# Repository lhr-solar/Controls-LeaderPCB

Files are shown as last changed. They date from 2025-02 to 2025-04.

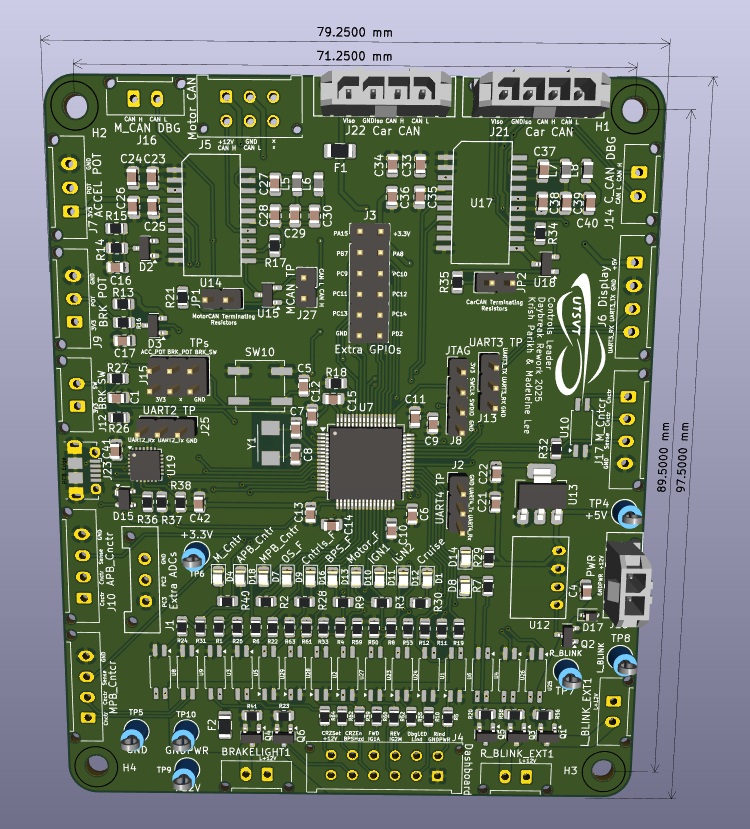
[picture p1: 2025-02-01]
Controls-Leader.png

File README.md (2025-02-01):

# Electronics : SCH/PCB
Contains all schematics and PCB files for the electrical system. Some teams may use the Solar Google Drive to upload their files.

------ 2025 Daybreak Controls Leaderboard ------
Purpose: Run main Controls code and interface with the motor controller and other systems through CAN.
Mouser link BOM: <to come>
List of components taking up volume outside of board dimensions
- Molex connectors along the entire perimeter (and one slightly inside) of the board
- Pin headers on the board
LEDs:
- Cruise controls is on
- Controls has a fault
- BPS has sent a fault
- Motor controller sent a fault
- Array precharge bypass contactor pin is high
- Motor precharge bypass contactor pin is high
- Motor contactor pin is high
-

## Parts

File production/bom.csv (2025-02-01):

Designator | Footprint | Quantity | Value | LCSC Part #
BRAKELIGHT1 | Molex_Micro-Fit_3.0_43650-0215_1x02_P3.00mm_Vertical | 1 | EXTERNAL_BRAKELIGHT
C1, C15 | 0805 | 2 | 1uF
C10, C13, C41 | 0805 | 3 | 4.7uF
C11, C12, C14, C5, C6, C9 | 0805 | 6 | 100nF
C16, C17, C24, C25, C29, C34, C35, C39, C42 | 0805 | 9 | 0.1uF
C21, C22, C4 | 0805 | 3 | 10u
C23, C28, C33, C38 | 0805 | 4 | 10uF
C26, C30, C36, C40 | 0805 | 4 | 0.01uF
C27, C37 | 0805 | 2 | 0.22uF
C7, C8 | 0805 | 2 | 12pF
D1 | 0805 | 1 | Cruise Ind
D10 | 0805 | 1 | Motor Controller Fault
D11 | 0805 | 1 | Ignition 1
D12 | 0805 | 1 | Ignition 2
D13 | 0805 | 1 | BPS Fault
D14, D8 | 0805 | 2 | PowerOn
D15 | SOT-143 | 1 | SP0503BAHTG
D16 | 0805 | 1 | Control Fault
D17 | D_SOD-323 | 1 | SD12_SOD323
D18 | 0805 | 1 | APB_CNCTR
D2, D3 | SOT-23 | 2 | BAS70-04
D4 | 0805 | 1 | M_CNCTR
D7 | 0805 | 1 | MPB_CNCTR
D9 | 0805 | 1 | OS Error
F1, F2 | 1206 | 2 | Fuse
H1, H2, H3, H4 | MountingHole_3mm | 4 | MountingHole
J1 | Molex_MicroFit3.0_1x3xP3.00mm_PolarizingPeg_Vertical | 1 | ExtraADCs
J10 | Molex_Micro-Fit_3.0_43650-0415_1x04_P3.00mm_Vertical | 1 | A_PRCHG_BYPASS
J11 | Molex_Micro-Fit_3.0_43650-0415_1x04_P3.00mm_Vertical | 1 | M_PRCHG_BYPASS
J12 | Molex_Micro-Fit_3.0_43650-0215_1x02_P3.00mm_Vertical | 1 | Brake_Sw
J13, J2, J25 | PinHeader_1x03_P2.54mm_Vertical | 3 | UART_TP
J14 | Molex_Micro-Fit_3.0_43650-0215_1x02_P3.00mm_Vertical | 1 | CAN_DB9
J15 | PinHeader_2x03_P2.54mm_Vertical | 1 | Conn_02x03_Odd_Even
J16 | Molex_Micro-Fit_3.0_43650-0215_1x02_P3.00mm_Vertical | 1 | M_CAN_DB9
J17 | Molex_Micro-Fit_3.0_43650-0415_1x04_P3.00mm_Vertical | 1 | M_CNTCTR
J18 | Molex_MicroFit3.0_1x2xP3.00mm_PolarizingPeg_Vertical | 1 | PowerConn
J21 | Molex_MicroFit3.0_1x4xP3.00mm_PolarizingPeg_Vertical | 1 | CAN_IN
J22 | Molex_MicroFit3.0_1x4xP3.00mm_PolarizingPeg_Vertical | 1 | CAN_OUT
J23 | USB_Micro-B_Molex-105017-0001 | 1 | USB_B_Micro
J27 | PinHeader_1x02_P2.54mm_Vertical | 1 | CAN_TP
J3 | PinHeader_2x06_P2.54mm_Vertical | 1 | ExtraGPIO_Conn
J4 | Molex_MicroFit3.0_2x6xP3.00mm_PolarizingPeg_Vertical | 1 | Dashboard
J5 | Molex_Micro-Fit_3.0_43045-0612_2x03_P3.00mm_Vertical | 1 | M_CAN_IN
J6 | Molex_Micro-Fit_3.0_43650-0415_1x04_P3.00mm_Vertical | 1 | Display
J7 | Molex_Micro-Fit_3.0_43650-0315_1x03_P3.00mm_Vertical | 1 | Accel_Pot
J8 | PinHeader_1x04_P2.54mm_Vertical | 1 | SWD
J9 | Molex_Micro-Fit_3.0_43650-0315_1x03_P3.00mm_Vertical | 1 | Brake_Pot
JP1, JP2 | PinHeader_1x02_P2.54mm_Vertical | 2 | Termination Resistors
L5, L6, L7, L8 | 0805 | 4 | 1.8k
LOGO1 | Hallock_Image | 1 | Dr. Hallock
LOGO2 | UTSVT_Logo_Symbol | 1 | UTSVT
LOGO4 | UTSVT_Logo_Symbol | 1 | UTSVT Logo
L_BLINK_EXT1 | Molex_Micro-Fit_3.0_43650-0215_1x02_P3.00mm_Vertical | 1 | EXTERNAL_LEFTBLINK
Q1, Q2, Q3, Q4, Q5, Q6 | SOT-23 | 6 | IRLML0030
R1, R2, R28, R3, R30, R31, R4, R40, R8, R9 | 0805 | 10 | 698
R10, R39, R5, R52, R55, R60, R62, R64 | 0805 | 8 | 2k
R11, R12, R19, R22, R6 | 0805 | 5 | 510
R13, R7 | 0805 | 2 | 5.1k
R14, R20, R23, R41, R56, R58 | 0805 | 6 | 100k
R15, R33, R50, R53, R59, R61, R63 | 0805 | 7 | 4.9k
R16, R18, R26, R27 | 0805 | 4 | 10k
R17, R34 | 0805 | 2 | 0
R21, R35 | 0805 | 2 | 120
R24, R25, R32 | 0805 | 3 | 105R
R29 | 0805 | 1 | 1.5k
R36 | 0805 | 1 | 22.1k
R37 | 0805 | 1 | 47.5k
R38 | 0805 | 1 | 1k
R_BLINK_EXT1 | Molex_Micro-Fit_3.0_43650-0215_1x02_P3.00mm_Vertical | 1 | EXTERNAL_RIGHTBLINK
SW10 | SW_SPST_B3SL-1002P | 1 | RESET
TP10 | TestPoint_Keystone_5005-5009_Compact | 1 | GND_UNISO
TP4 | TestPoint_Keystone_5005-5009_Compact | 1 | +5V_TP
TP5 | TestPoint_Keystone_5005-5009_Compact | 1 | GND_TP
TP6 | TestPoint_Keystone_5005-5009_Compact | 1 | +3.3V_TP
TP7 | TestPoint_Keystone_5005-5009_Compact | 1 | RIGHT_BLINK
TP8 | TestPoint_Keystone_5005-5009_Compact | 1 | LEFT_BLINK
TP9 | TestPoint_Keystone_5005-5009_Compact | 1 | 12V_UNISO
U1, U10, U2, U23, U24, U25, U26, U27, U28, U29, U3, U4, U5, U6, U8, U9 | SSOP-4_4.4x2.6mm_P1.27mm | 16 | EL3H7
U12 | RI3_DC_Converter | 1 | RI3-1205S
U13 | SOT-223-3_TabPin2 | 1 | NCP1117-3.3_SOT223
U14, U17 | SOIC-20W_7.5x15.4mm_Pitch1.27mm | 2 | ADM3055E
U15, U18 | SOT-23-3 | 2 | CDSOT23-T24CAN
U19 | QFN-24-1EP_4x4mm_P0.5mm_EP2.6x2.6mm | 1 | CP2102N-A01-GQFN24
U7 | LQFP-64_10x10mm_P0.5mm | 1 | STM32F413RHTx
Y1 | Crystal_SMD_TXC_7A-2Pin_5x3.2mm | 1 | Crystal

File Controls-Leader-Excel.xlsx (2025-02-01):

Reference | Value | Qty | P/N
BRAKELIGHT1,J16,L_BLINK_EXT1,R_BLINK_EXT1 | -- mixed values -- | 4 | 43650-0215
C1,C15 | 1uF | 2 | C0805C105J3RECAUTO
C4,C21,C22,C23,C28,C33,C38 | 10uF | 7 | TMK212BBJ106MGHT
C5,C6,C9,C11,C12,C14,C16,C17,C24,C25,C29,C34,C35,C39,C42 | 0.1uF | 15 | C0805C104M5R
C7,C8 | 12pF | 2 | C0805C120K5HACTU
C10,C13,C41 | 4.7uF | 3 | GRM219R6YA475KA3D
C26,C30,C36,C40 | 0.01uF | 4 | C0805C103J5RACTU
C27,C37 | 0.22uF | 2 | C0805C224J1RECTU
D1,D4,D7,D8,D9,D10,D11,D12,D13,D14,D16,D18 | -- mixed values -- | 12 | APTD2012LCGCK
D2,D3 | BAS70-04 | 2 | CDSOT23-T24CAN
D15 | SP0503BAHTG | 1 | SP0503BAHTG
D17 | SD12_SOD323 | 1 | SD12C.TCT
F1 | Fuse | 1 | 0440.375WR
F2 | Fuse | 1 | 0440003.WR
H1,H2,H3,H4,J2,J3,J8,J13,J15,J25,J27,JP1,JP2,LOGO1,LOGO2,LOGO4,TP4,TP5,TP6,TP7,TP8,TP9,TP10 | -- mixed values -- | 23
J1,J7,J9 | -- mixed values -- | 3 | 436500315
J4 | Dashboard | 1 | 430451212
J5 | M_CAN_IN | 1 | 430450626
J6,J10,J11,J17,J21,J22 | -- mixed values -- | 6 | 436500244
J12,J14,J18 | -- mixed values -- | 3 | 436500215
J23 | USB_B_Micro | 1 | 105017-1001
L5,L6,L7,L8 | 1.8k | 4 | 742792090
Q1,Q2,Q3,Q4,Q5,Q6 | IRLML0030 | 6 | IRLML0030TRPBF
R1,R2,R3,R4,R8,R9,R28,R30,R31,R40 | 698 | 10 | CR0805-FX-6980ELF
R5,R10,R39,R52,R55,R60,R62,R64 | 2k | 8 | CRCW08052K00FKEC
R6,R11,R12,R19,R22 | 510 | 5 | CRCW0805510RFKEAC
R7,R13 | 5.1k | 2 | Inventory
R14,R20,R23,R41,R56,R58 | 100k | 6 | CRCW0805100KFKEAC
R15,R33,R50,R53,R59,R61,R63 | 4.9k | 7 | CRCW08054K99FKEAC
R16,R18,R26,R27 | 10k | 4 | CRCW080510K0FKEAC
R17,R34 | 0 | 2 | CRCW08050000Z0EAC
R21,R35 | 120 | 2 | CRCW0805120RFKEA
R24,R25,R32 | 105R | 3 | CRCW0805105RFKEA
R29 | 1.5k | 1 | CRCW08051K50JNEB
R36 | 22.1k | 1 | CRCW0805-22.1K-E3
R37 | 47.5k | 1 | CRCW0805-47.5K-E3
R38 | 1k | 1 | CRCW08051K00FKEAC
SW10 | RESET | 1 | B3SL-1002P
U1,U2,U3,U4,U5,U6,U8,U9,U10,U23,U24,U25,U26,U27,U28,U29 | EL3H7 | 16 | EL3H7DTAVG
U7 | STM32F413RHTx | 1 | STM32F413RHT6
U12 | RI3-1205S | 1 | RI3-1205S
U13 | NCP1117-3.3_SOT223 | 1 | NCP1117ST33T3G
U14,U17 | ADM3055E | 2 | ADM3055E
U15,U18 | CDSOT23-T24CAN | 2 | CDSOT23-T24CAN
U19 | CP2102N-A02-GQFN24 | 1 | CP2102N-A02-GQFN24
Y1 | Crystal | 1 | ABM3-8.000MHZ-D2Y-T

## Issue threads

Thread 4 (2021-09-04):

Power Input Protection Circuitry

babusid, 2021-09-04:
During the course of testing, a power supply was plugged improperly into the controls leaderboard (+12v was connected to the ground line, and the ground was connected to the +12v line on the board), and ended up blowing the 12v->5v power regulator. We need a protection circuit ahead of the regulator in order to prevent that mistake from damaging the board.

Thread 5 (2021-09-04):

External Lights Output terminal polarity reverse

babusid, 2021-09-04:
Output Terminals on the external lights output are currently reversed in polarity and need to be flipped in the Rev 2 board.

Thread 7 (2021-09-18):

CAN2 -> CAN3

JimothyGreene, 2021-09-18:
We need to move the Motor CAN bus to use CAN3 instead of CAN2. The CAN2 design used PB12 and PB13 for Rx/Tx respectively. The new design needs to use PA8 and PA15 for Rx/Tx respectively. This will require the JTDI connection to be removed from PA15, which is not a problem since we don't actually use JTAG to program the board. We can also just remove JTDO as well while we're in this process.

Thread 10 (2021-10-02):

ADC uC pin

JimothyGreene, 2021-10-02:
Remap ADC pins. New potentiometer pins should be PC0:3 and switch contactors and precharge to old ADC locations.

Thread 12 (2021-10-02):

isoSPI Driver Short

JimothyGreene, 2021-10-02:
Short between 14-16 on driver IC

Closed 2021-10-03.

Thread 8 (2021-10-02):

12V Separation

JimothyGreene, 2021-10-02:
There are 2 12V inputs to the board. One is from primary power and the other is from secondary power. They should be labeled as such.

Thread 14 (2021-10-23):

12V CAN Motor Connection

HannahSLee14, 2021-10-23:
Motor CAN Connector has iso_5V and iso_GND connected to it instead of iso_12V and iso_GND, which is required by the motor. We need to add a 12V to 12V isolated DC-DC Converter and connect the output to these to the Motor CAN Connector.

HannahSLee14, 2021-11-06:
Ideally,  the 12V to 12V isolated DC-DC Converter would be the [RI3-1212S](https://www.mouser.com/ProductDetail/RECOM-Power/RI3-1212S?qs=IbBl3rwNelNtmsZ9Y1jE4w%3D%3D) so we can use the same footprint, but we should check the specs and needs just in case.

Closed 2022-05-01.

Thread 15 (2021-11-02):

Change isoSPI -> SPI

HannahSLee14, 2021-11-02:
Since isoSPI is giving us a lot of issues, we are going to remove the chips associated with isoSPI (LTC6820 and HX1188FNL) and any components that are a part of its circuitry. We are going to send out the SPI signals instead (MISO, MOSI, CLK, CS).

** We should check the number of wires we can have in the steering wheel disconnect. **

Closed 2022-05-01.

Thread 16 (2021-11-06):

Ignition Switch Current-Limiting Resistor

JimothyGreene, 2021-11-06:
The optocouplers attached to the ignition switch circuit need current-limiting resistors in series. Look at the other uses of these optocouplers in this board for examples.

HannahSLee14, 2021-11-06:
Value on the old schematic is 540 ohms.

Closed 2022-05-01.

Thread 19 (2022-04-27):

POR circuitry

babusid, 2022-04-27:
We're having weird issues with behavior on chip reset being different than behavior on power cycle. This could be caused by chips coming on at different points in the voltage ramp after power cycle (ie. STM comes online sooner than some peripheral chips, and immediate initializations fail as a result). Including POR circuitry on the leader board would ensure that the STM only starts executing instructions once we're past a certain voltage threshold to ensure that program execution begins after all chips are on.

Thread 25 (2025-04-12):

UART, Silkscreen labeled incorrectly

KnockbackNemo, 2025-04-12:
Some of the schematic/silkscreen labels are incorrect.

Schematic: (Should probably change this on the schematic)
UART2 should be labeled as USART2
UART3 should be UART4
UART4 should be UART5

Silkscreen: (Consider labeling this on the board?)
ExtraADCs GND should be ExtraADC1 (PC2)
ExtraADCs PC2 should be PC3
ExtraADCs PC3 should be GND

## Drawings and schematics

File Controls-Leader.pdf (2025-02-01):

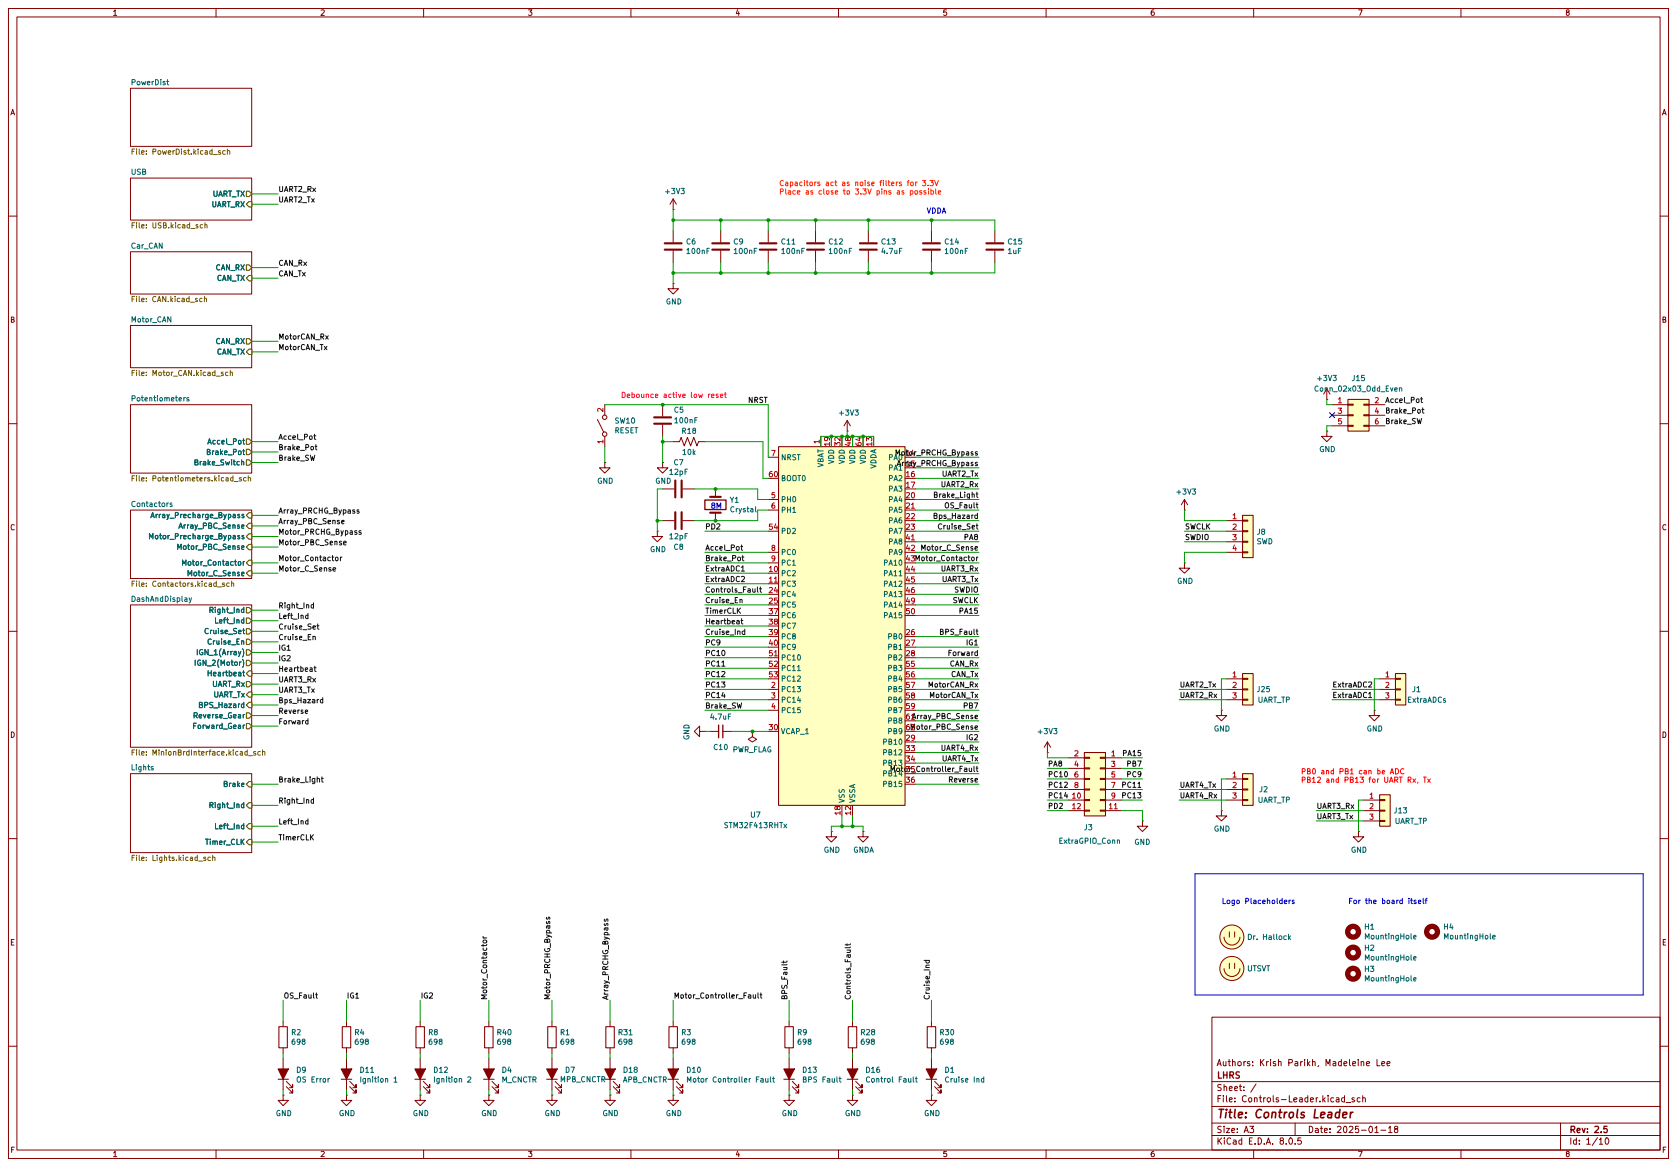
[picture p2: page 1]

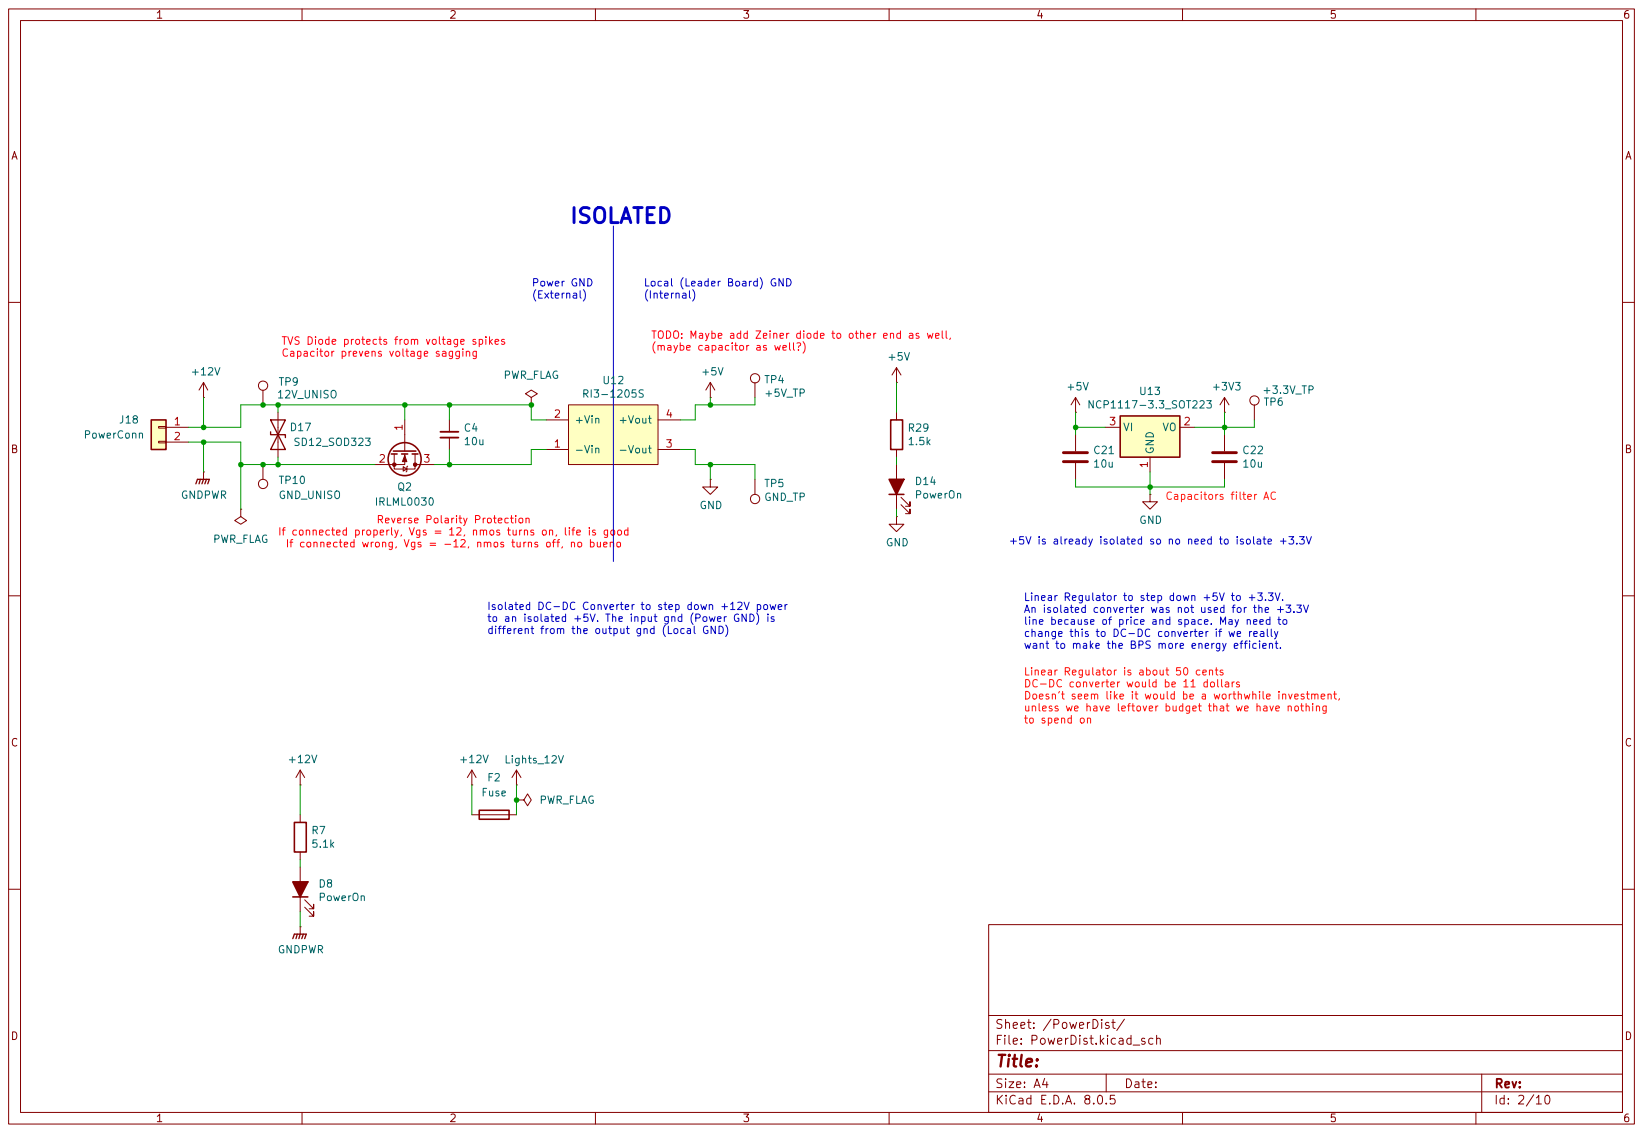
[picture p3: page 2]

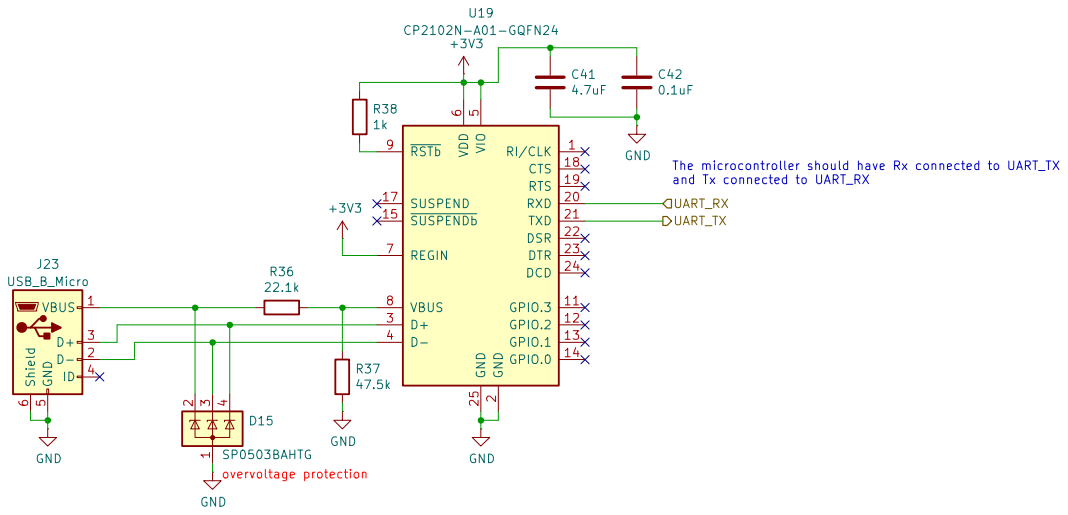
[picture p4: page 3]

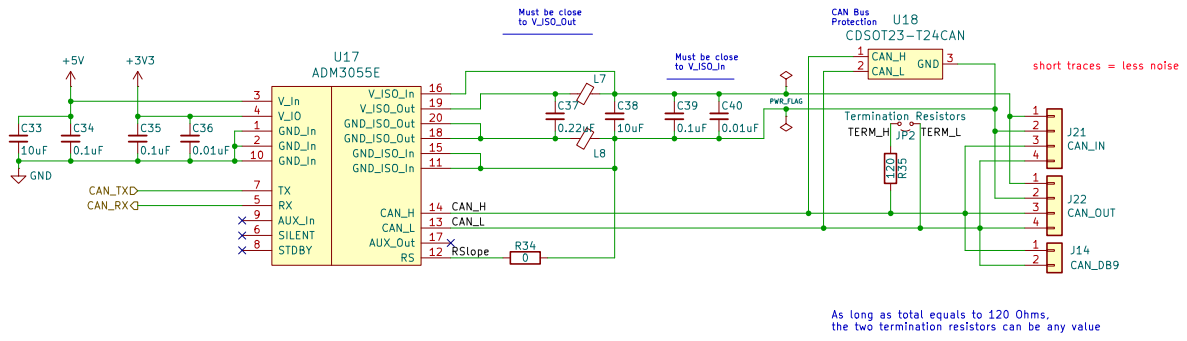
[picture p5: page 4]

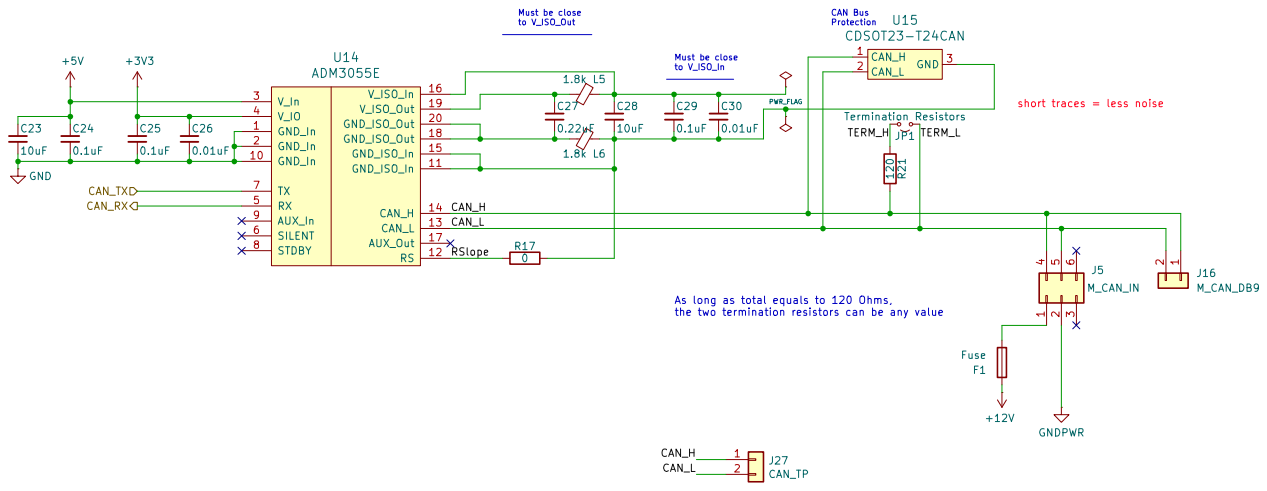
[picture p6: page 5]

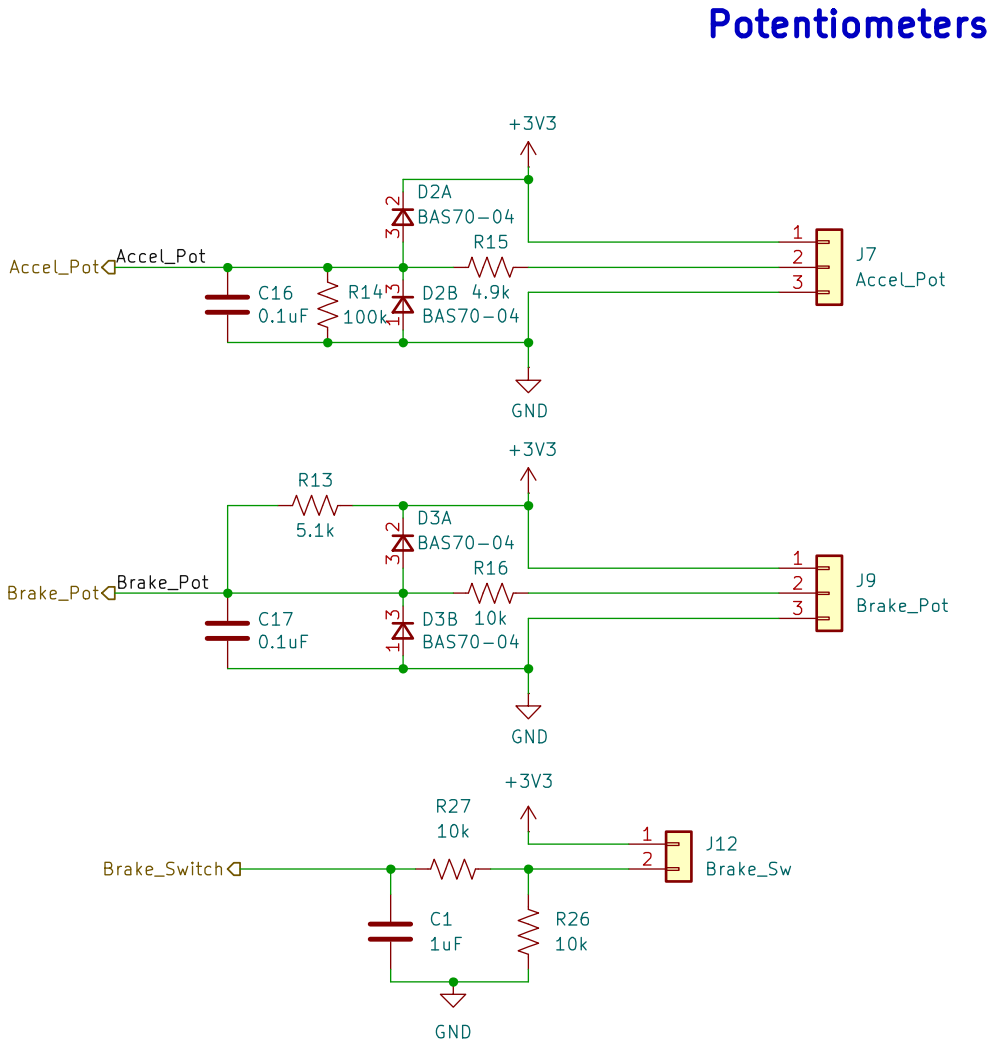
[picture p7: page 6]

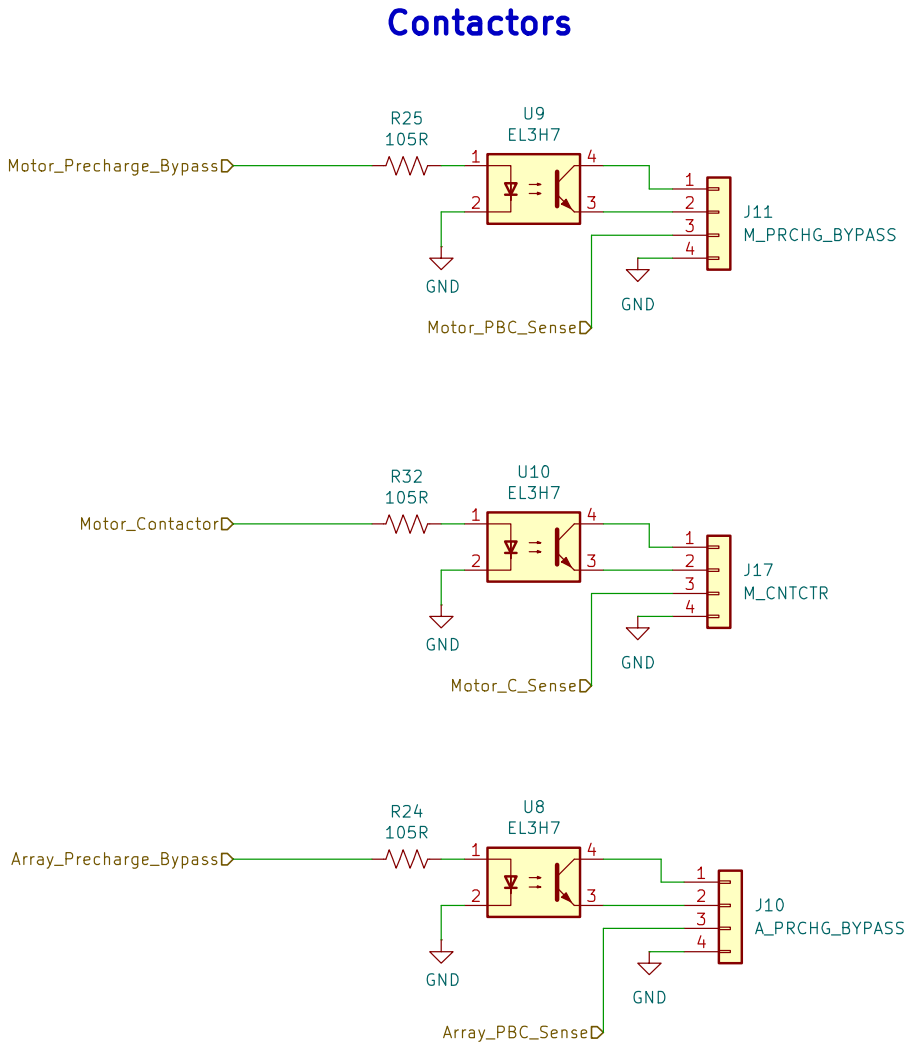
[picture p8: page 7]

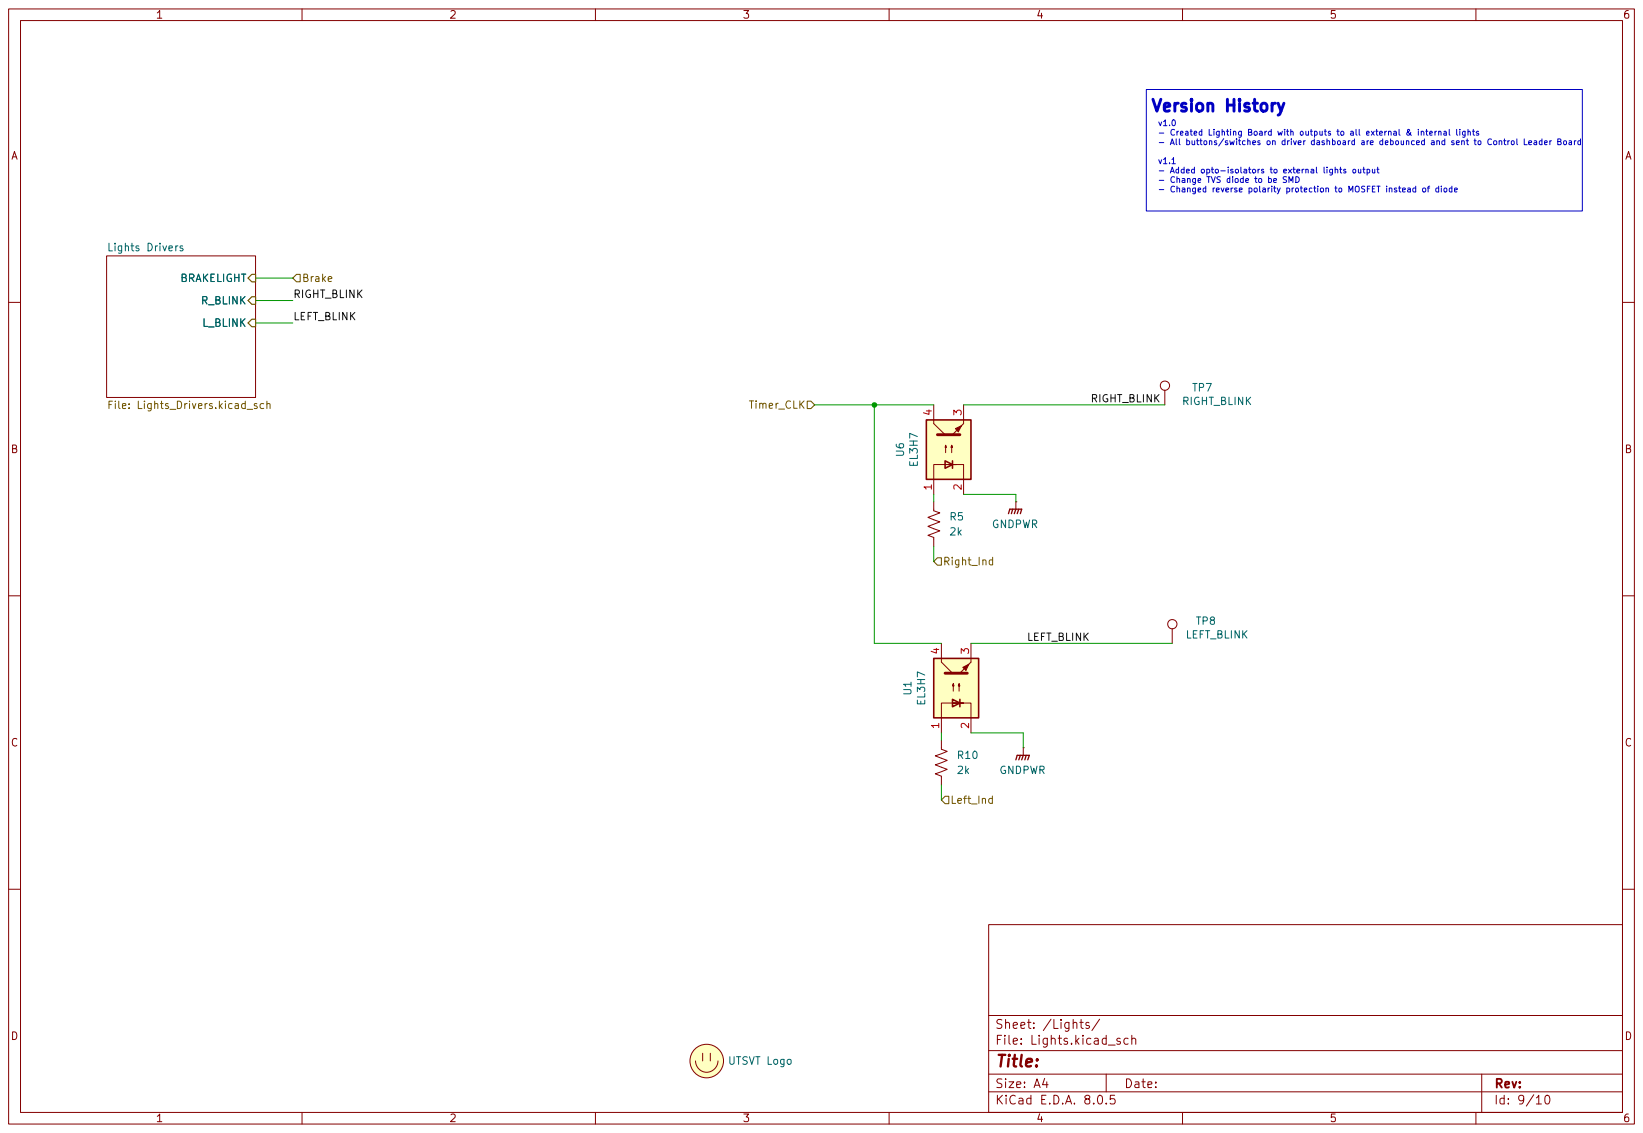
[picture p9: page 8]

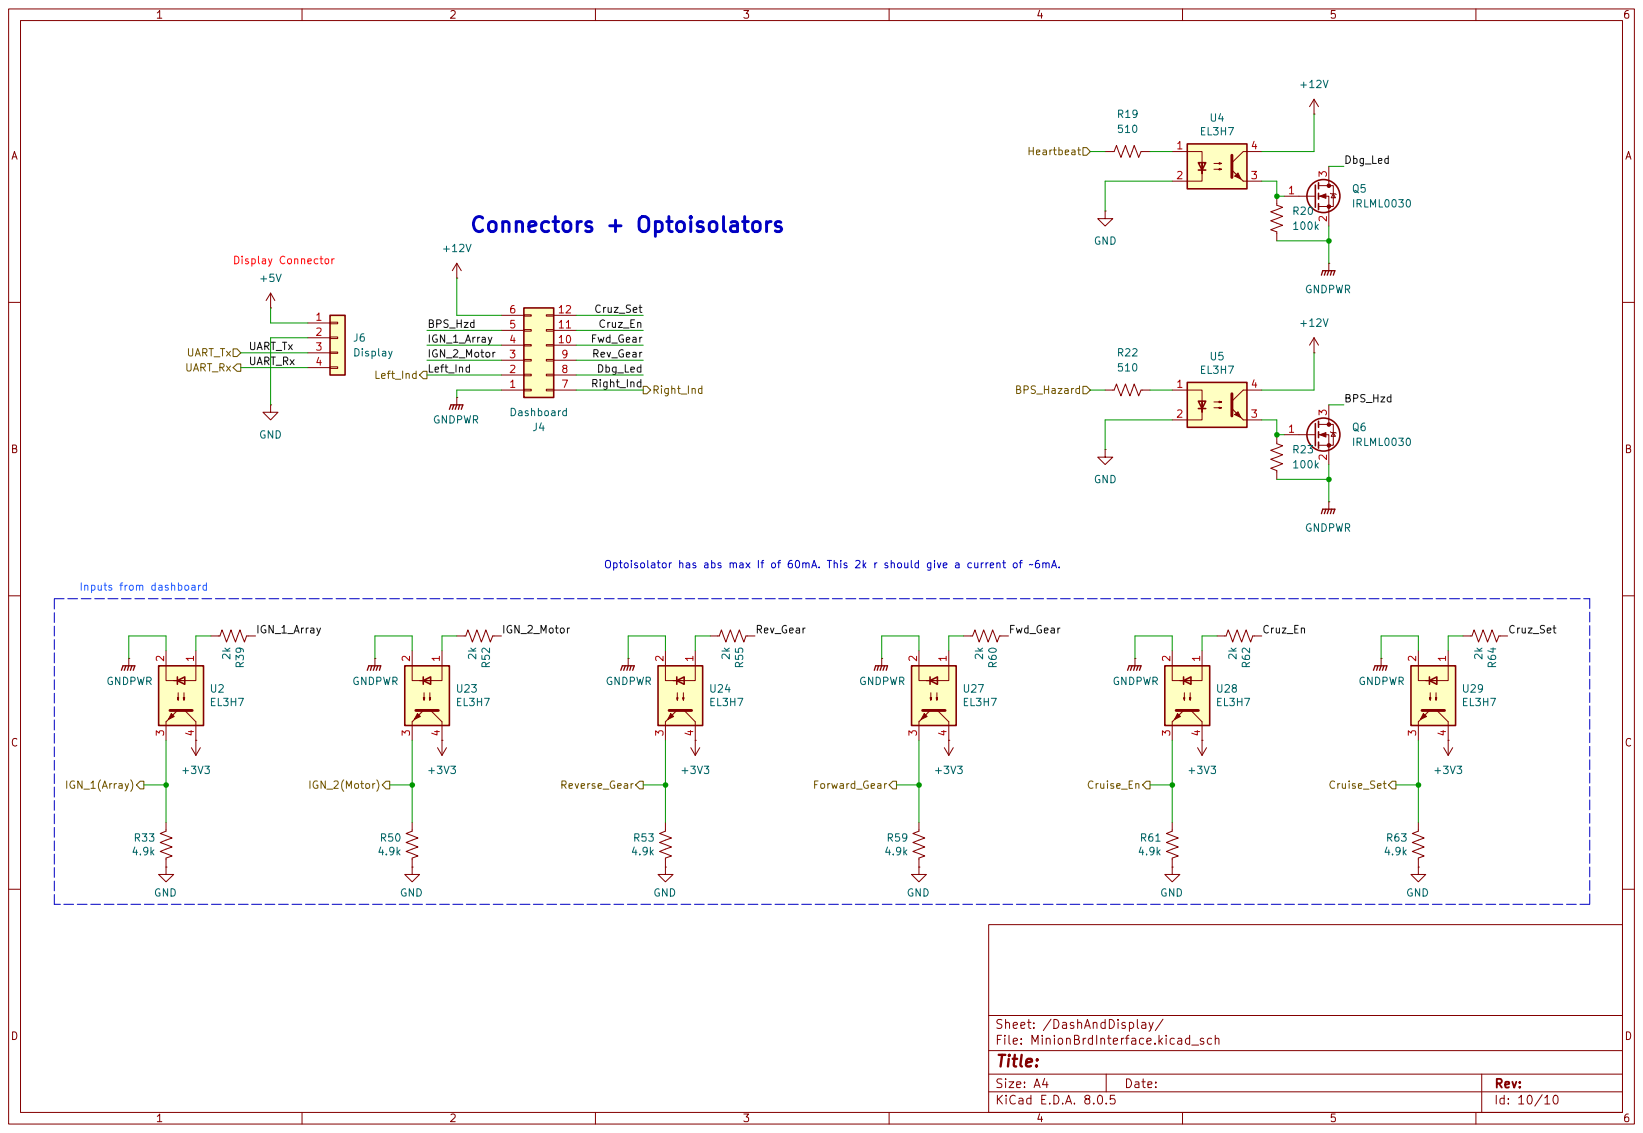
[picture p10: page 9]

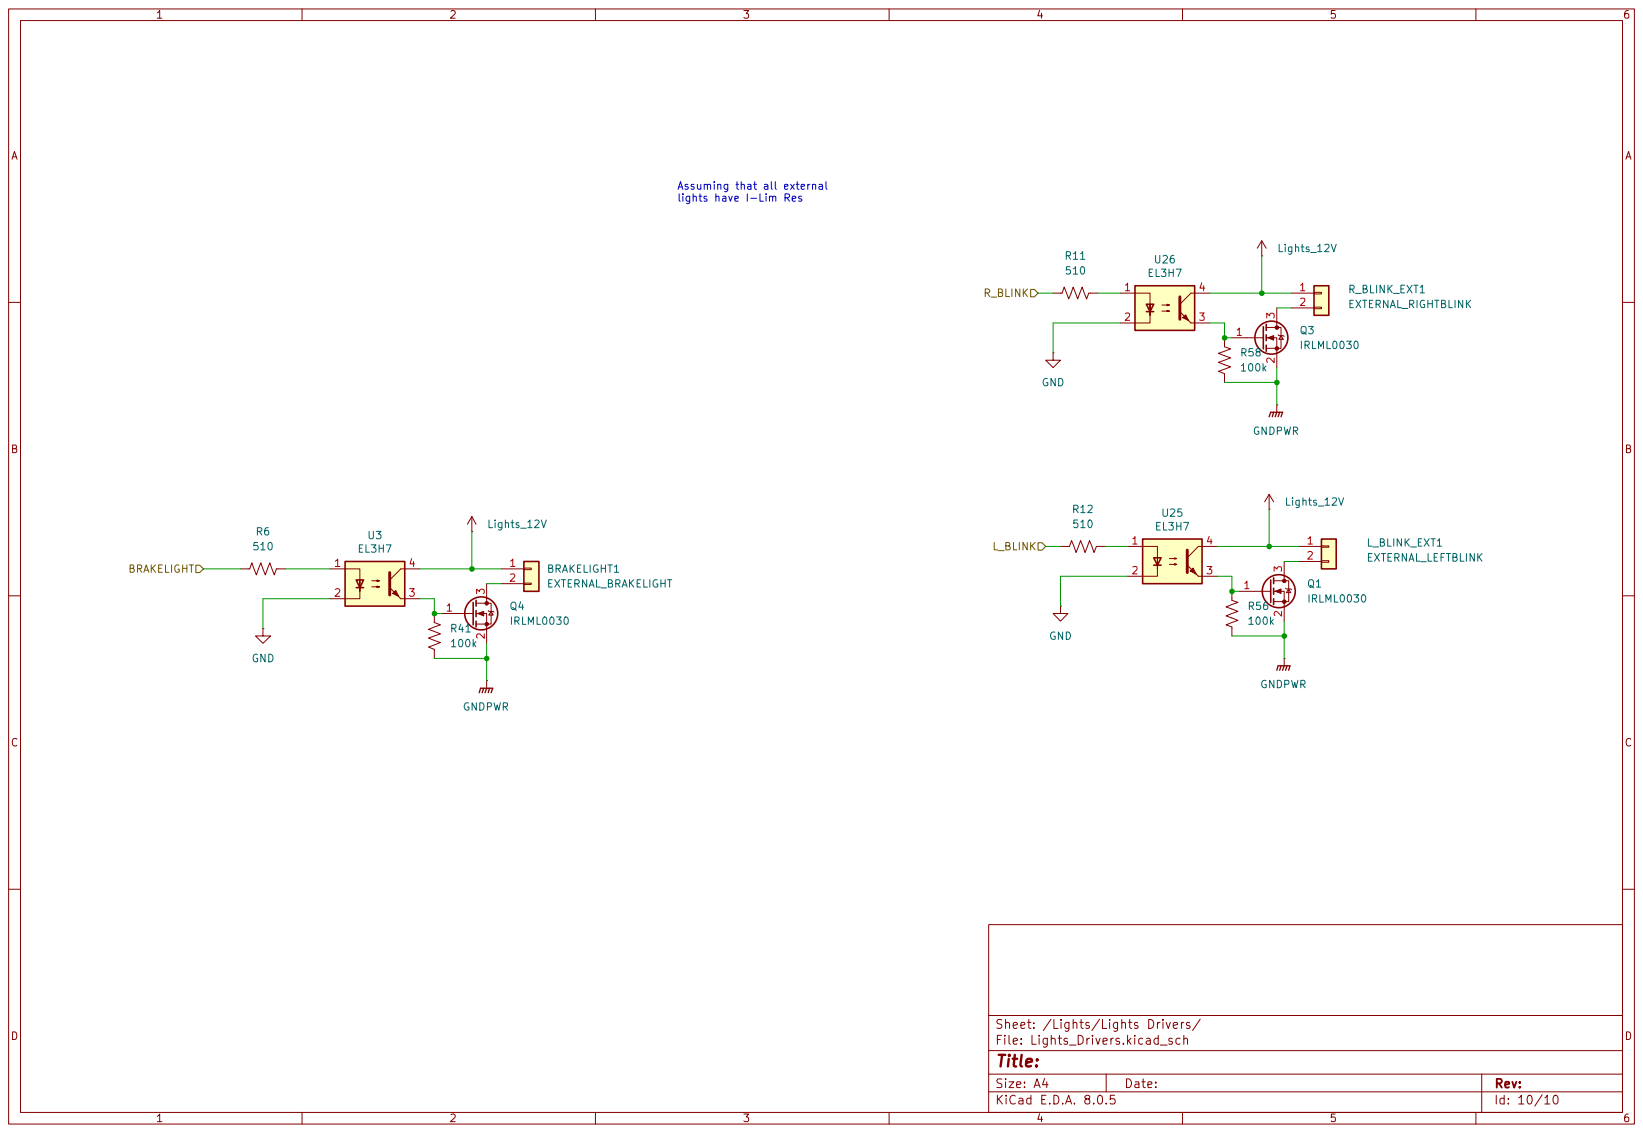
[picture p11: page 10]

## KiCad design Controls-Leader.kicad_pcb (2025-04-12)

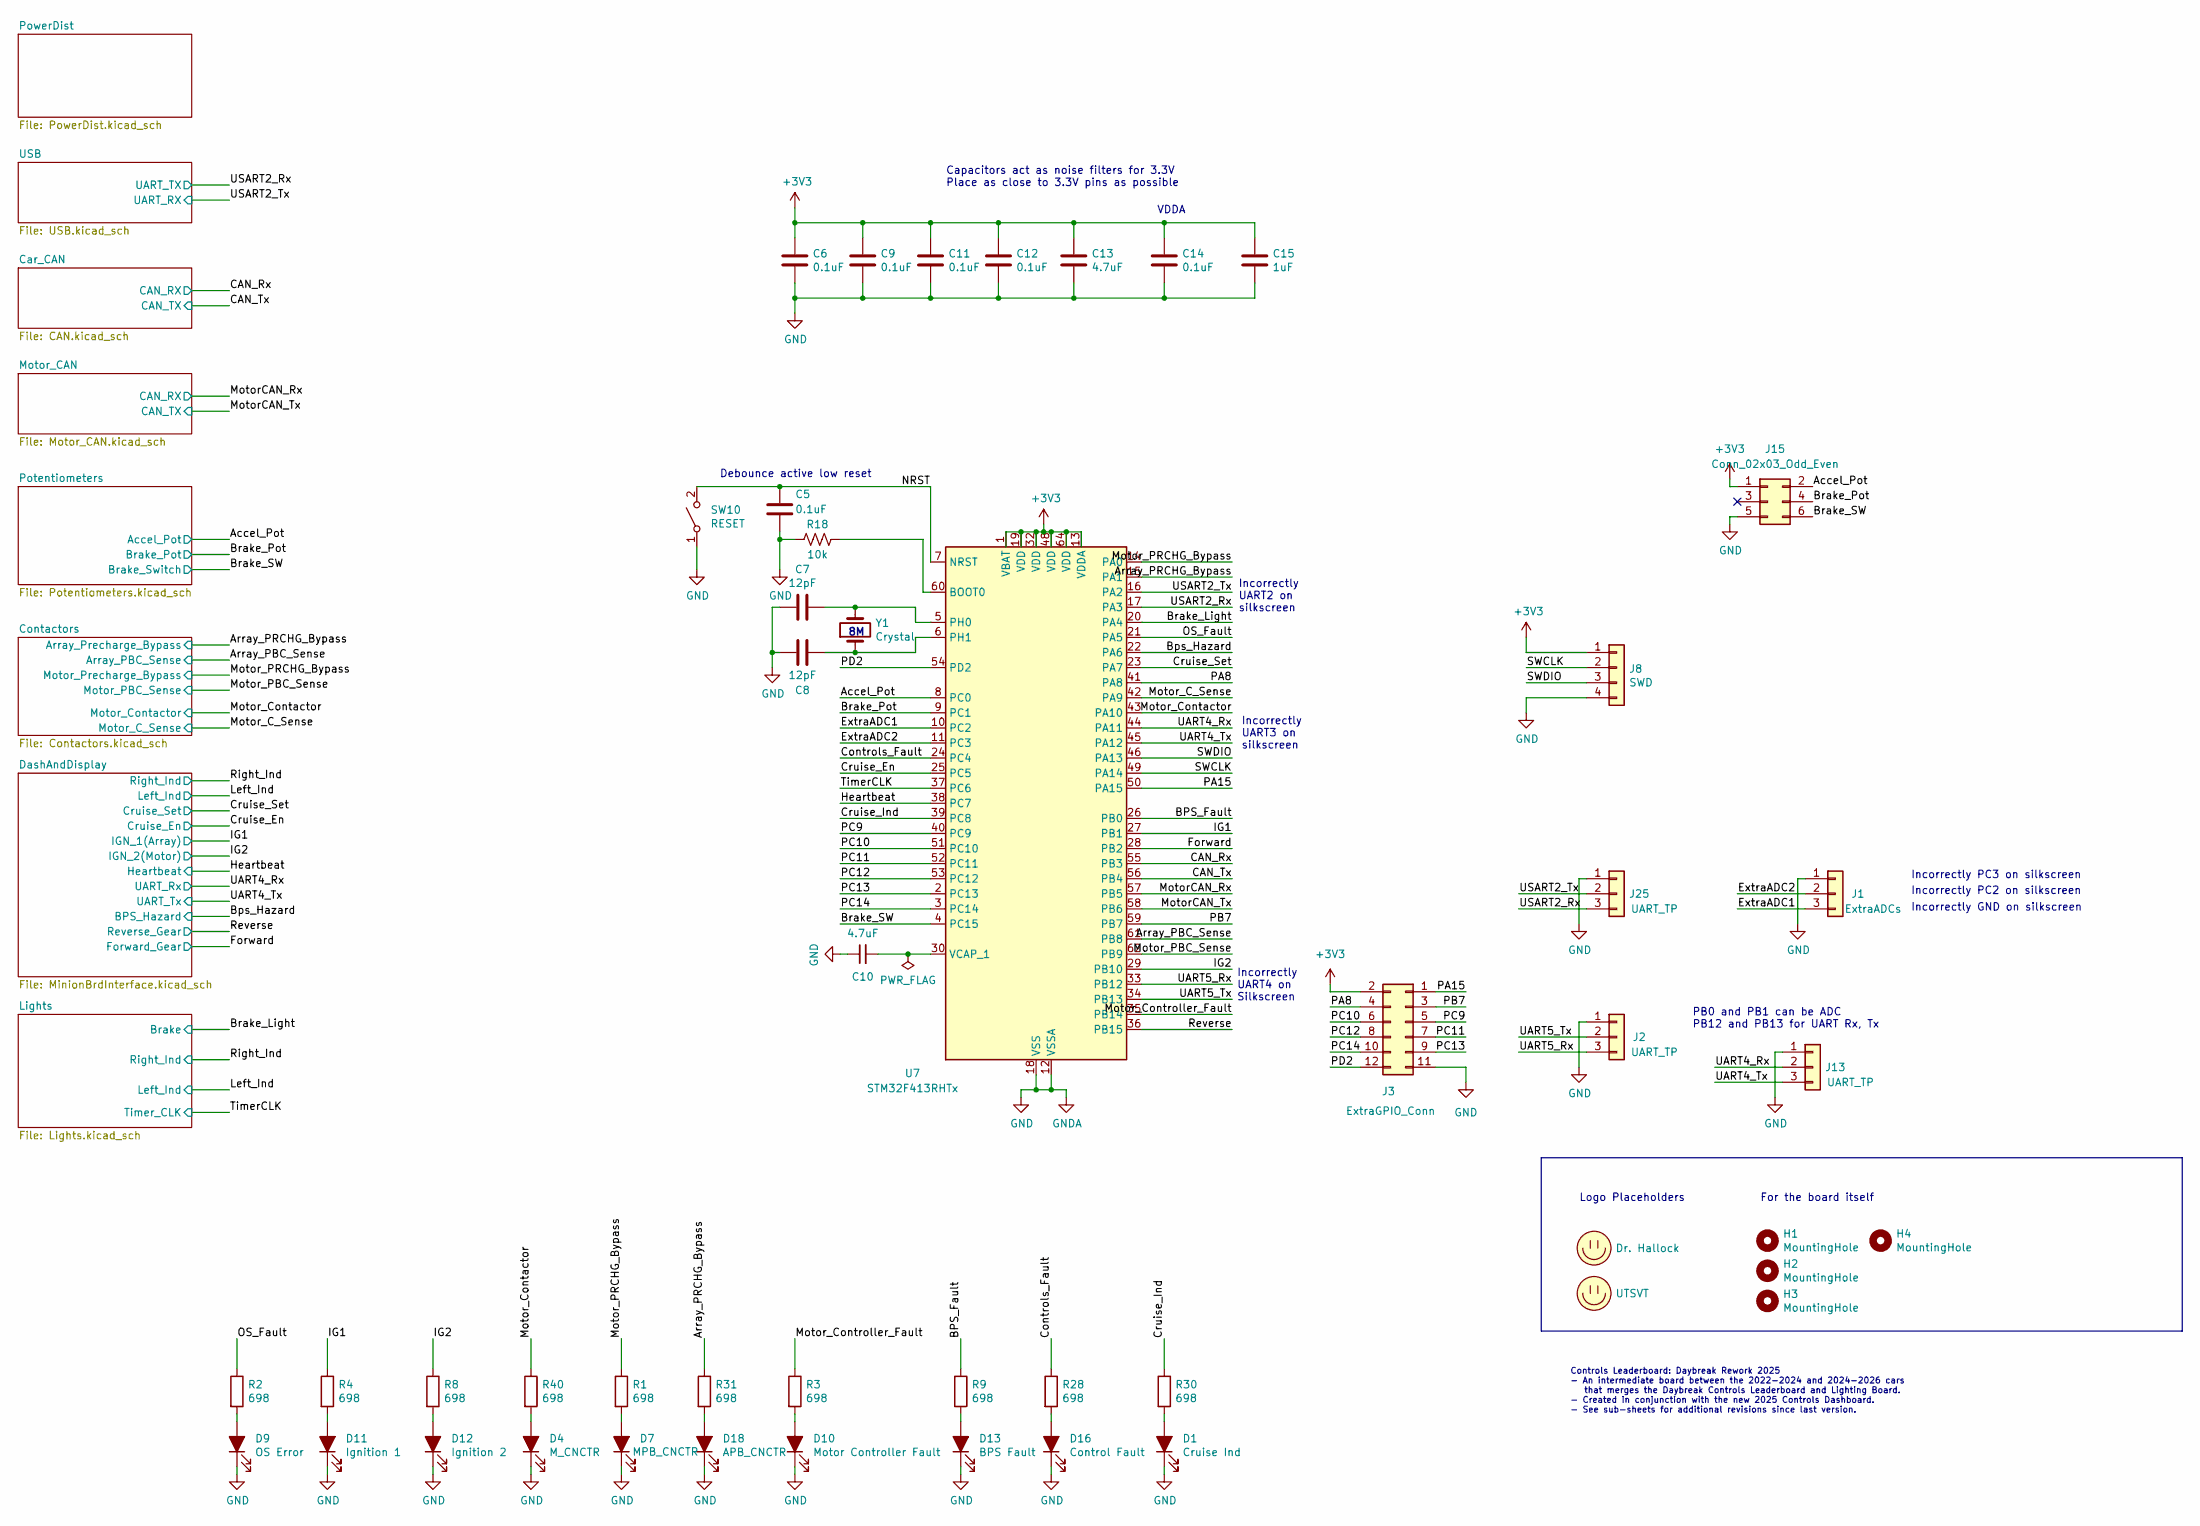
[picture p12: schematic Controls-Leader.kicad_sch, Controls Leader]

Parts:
C5, C6, C9, C11, C12, C14: 0.1uF; C_0805_2012Metric; Mouser Part Number 80-C0805C104M5R
C7, C8: 12pF; C_0805_2012Metric; Mouser Part Number 80-C0805C120K5HACTU
C10, C13: 4.7uF; C_0805_2012Metric; Mouser Part Number 81-GRM219R6YA475KA3D
C15: 1uF; C_0805_2012Metric
D1: Cruise Ind; LED_0805_2012Metric; Mouser Part Number 604-APTD2012LCGCK
D4: M_CNCTR; LED_0805_2012Metric; Mouser Part Number 604-APTD2012LCGCK
D7: MPB_CNCTR; LED_0805_2012Metric; Mouser Part Number 604-APTD2012LCGCK
D9: OS Error; LED_0805_2012Metric; Mouser Part Number 604-APTD2012LCGCK
D10: Motor Controller Fault; LED_0805_2012Metric; Mouser Part Number 604-APTD2012LCGCK
D11: Ignition 1; LED_0805_2012Metric; Mouser Part Number 604-APTD2012LCGCK
D12: Ignition 2; LED_0805_2012Metric; Mouser Part Number 604-APTD2012LCGCK
D13: BPS Fault; LED_0805_2012Metric; Mouser Part Number 604-APTD2012LCGCK
D16: Control Fault; LED_0805_2012Metric; Mouser Part Number 604-APTD2012LCGCK
D18: APB_CNCTR; LED_0805_2012Metric; Mouser Part Number 604-APTD2012LCGCK
H1, H2, H3, H4: MountingHole; MountingHole_3mm
J1: ExtraADCs; Molex_MicroFit3.0_1x3xP3.00mm_PolarizingPeg_Vertical
J2, J13, J25: UART_TP; PinHeader_1x03_P2.54mm_Vertical
J3: ExtraGPIO_Conn; PinHeader_2x06_P2.54mm_Vertical
J8: SWD; PinHeader_1x04_P2.54mm_Vertical
J15: Conn_02x03_Odd_Even; PinHeader_2x03_P2.54mm_Vertical
LOGO1: Dr. Hallock; Hallock_Image
LOGO2: UTSVT; UTSVT_Logo_Symbol
R1, R2, R3, R4, R8, R9, R28, R30, R31, R40: 698; R_0805_2012Metric; Mouser Part Number 652-CR0805FX-6980ELF
R18: 10k; R_0805_2012Metric; Mouser Part Number 71-CRCW080510K0FKEAC
SW10: RESET; SW_SPST_B3SL-1002P; Mouser Part Number 653-B3SL-1002P
U7: STM32F413RHTx; LQFP-64_10x10mm_P0.5mm; Mouser Part Number 511-STM32F413RHT6
Y1: Crystal; Crystal_SMD_TXC_7A-2Pin_5x3.2mm

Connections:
+3V3: C6.1, C9.1, C11.1, C12.1, C13.1, C14.1, C15.1, J3.2, J8.1, J15.1, U7.1 (VBAT), U7.13 (VDDA), U7.19 (VDD), U7.32 (VDD), U7.48 (VDD), U7.64 (VDD); also elsewhere on the board
/Accel_Pot: J15.2, U7.8 (PC0); also elsewhere on the board
/Array_PBC_Sense: U7.61 (PB8); also elsewhere on the board
/Array_PRCHG_Bypass: R31.1, U7.15 (PA1); also elsewhere on the board
/BPS_Fault: R9.1, U7.26 (PB0)
/Bps_Hazard: U7.22 (PA6); also elsewhere on the board
/Brake_Light: U7.20 (PA4); also elsewhere on the board
/Brake_Pot: J15.4, U7.9 (PC1); also elsewhere on the board
/Brake_SW: J15.6, U7.4 (PC15); also elsewhere on the board
/CAN_Rx: U7.55 (PB3); also elsewhere on the board
/CAN_Tx: U7.56 (PB4); also elsewhere on the board
/Controls_Fault: R28.1, U7.24 (PC4)
/Cruise_En: U7.25 (PC5); also elsewhere on the board
/Cruise_Ind: R30.1, U7.39 (PC8)
/Cruise_Set: U7.23 (PA7); also elsewhere on the board
/ExtraADC1: J1.3, U7.10 (PC2)
/ExtraADC2: J1.2, U7.11 (PC3)
/Forward: U7.28 (PB2); also elsewhere on the board
/Heartbeat: U7.38 (PC7); also elsewhere on the board
/IG1: R4.1, U7.27 (PB1); also elsewhere on the board
/IG2: R8.1, U7.29 (PB10); also elsewhere on the board
/MotorCAN_Rx: U7.57 (PB5); also elsewhere on the board
/MotorCAN_Tx: U7.58 (PB6); also elsewhere on the board
/Motor_C_Sense: U7.42 (PA9); also elsewhere on the board
/Motor_Contactor: R40.1, U7.43 (PA10); also elsewhere on the board
/Motor_Controller_Fault: R3.1, U7.35 (PB14)
/Motor_PBC_Sense: U7.62 (PB9); also elsewhere on the board
/Motor_PRCHG_Bypass: R1.1, U7.14 (PA0); also elsewhere on the board
/NRST: C5.1, SW10.2 (B), U7.7 (NRST)
/OS_Fault: R2.1, U7.21 (PA5)
/PA8: J3.4, U7.41 (PA8)
/PA15: J3.1, U7.50 (PA15)
/PB7: J3.3, U7.59 (PB7)
/PC9: J3.5, U7.40 (PC9)
/PC10: J3.6, U7.51 (PC10)
/PC11: J3.7, U7.52 (PC11)
/PC12: J3.8, U7.53 (PC12)
/PC13: J3.9, U7.2 (PC13)
/PC14: J3.10, U7.3 (PC14)
/PD2: J3.12, U7.54 (PD2)
/Reverse: U7.36 (PB15); also elsewhere on the board
/SWCLK: J8.2, U7.49 (PA14)
/SWDIO: J8.3, U7.46 (PA13)
/TimerCLK: U7.37 (PC6); also elsewhere on the board
/UART4_Rx: J13.2, U7.44 (PA11); also elsewhere on the board
/UART4_Tx: J13.3, U7.45 (PA12); also elsewhere on the board
/UART5_Rx: J2.3, U7.33 (PB12)
/UART5_Tx: J2.2, U7.34 (PB13)
/USART2_Rx: J25.3, U7.17 (PA3); also elsewhere on the board
/USART2_Tx: J25.2, U7.16 (PA2); also elsewhere on the board
GND: C5.2, C6.2, C7.2, C8.2, C9.2, C10.1, C11.2, C12.2, C13.2, C14.2, C15.2, D1.1 (K), D4.1 (K), D7.1 (K), D9.1 (K), D10.1 (K), D11.1 (K), D12.1 (K), D13.1 (K), D16.1 (K), D18.1 (K), J1.1, J2.1, J3.11, J8.4, J13.1, J15.5, J25.1, R18.2, SW10.1 (A), U7.12 (VSSA), U7.18 (VSS), U7.31 (VSS), U7.47 (VSS), U7.63 (VSS); also elsewhere on the board
unnamed: D1.2 (A), R30.2
unnamed: D4.2 (A), R40.2
unnamed: D7.2 (A), R1.2
unnamed: D9.2 (A), R2.2
unnamed: D10.2 (A), R3.2
unnamed: D11.2 (A), R4.2
unnamed: D12.2 (A), R8.2
unnamed: D13.2 (A), R9.2
unnamed: D16.2 (A), R28.2
unnamed: D18.2 (A), R31.2
unnamed: R18.1, U7.60 (BOOT0)
unnamed: C7.1, U7.5 (PH0), Y1.2
unnamed: C8.1, U7.6 (PH1), Y1.1
unnamed: C10.2, U7.30 (VCAP_1)

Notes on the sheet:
Incorrectly UART2 on silkscreen
Incorrectly GND on silkscreen
VDDA
PB0 and PB1 can be ADC PB12 and PB13 for UART Rx, Tx
Incorrectly PC3 on silkscreen
Incorrectly PC2 on silkscreen
Debounce active low reset
Incorrectly UART4 on Silkscreen
Logo Placeholders
Controls Leaderboard: Daybreak Rework 2025 - An intermediate board between the 2022-2024 and 2024-2026 cars that merges the Daybreak Controls Leaderboard and Lighting Board. - Created in conjunction with the new 2025 Controls Dashboard. - See sub-sheets for additional revisions since last version.
Incorrectly UART3 on silkscreen
Capacitors act as noise filters for 3.3V Place as close to 3.3V pins as possible
For the board itself

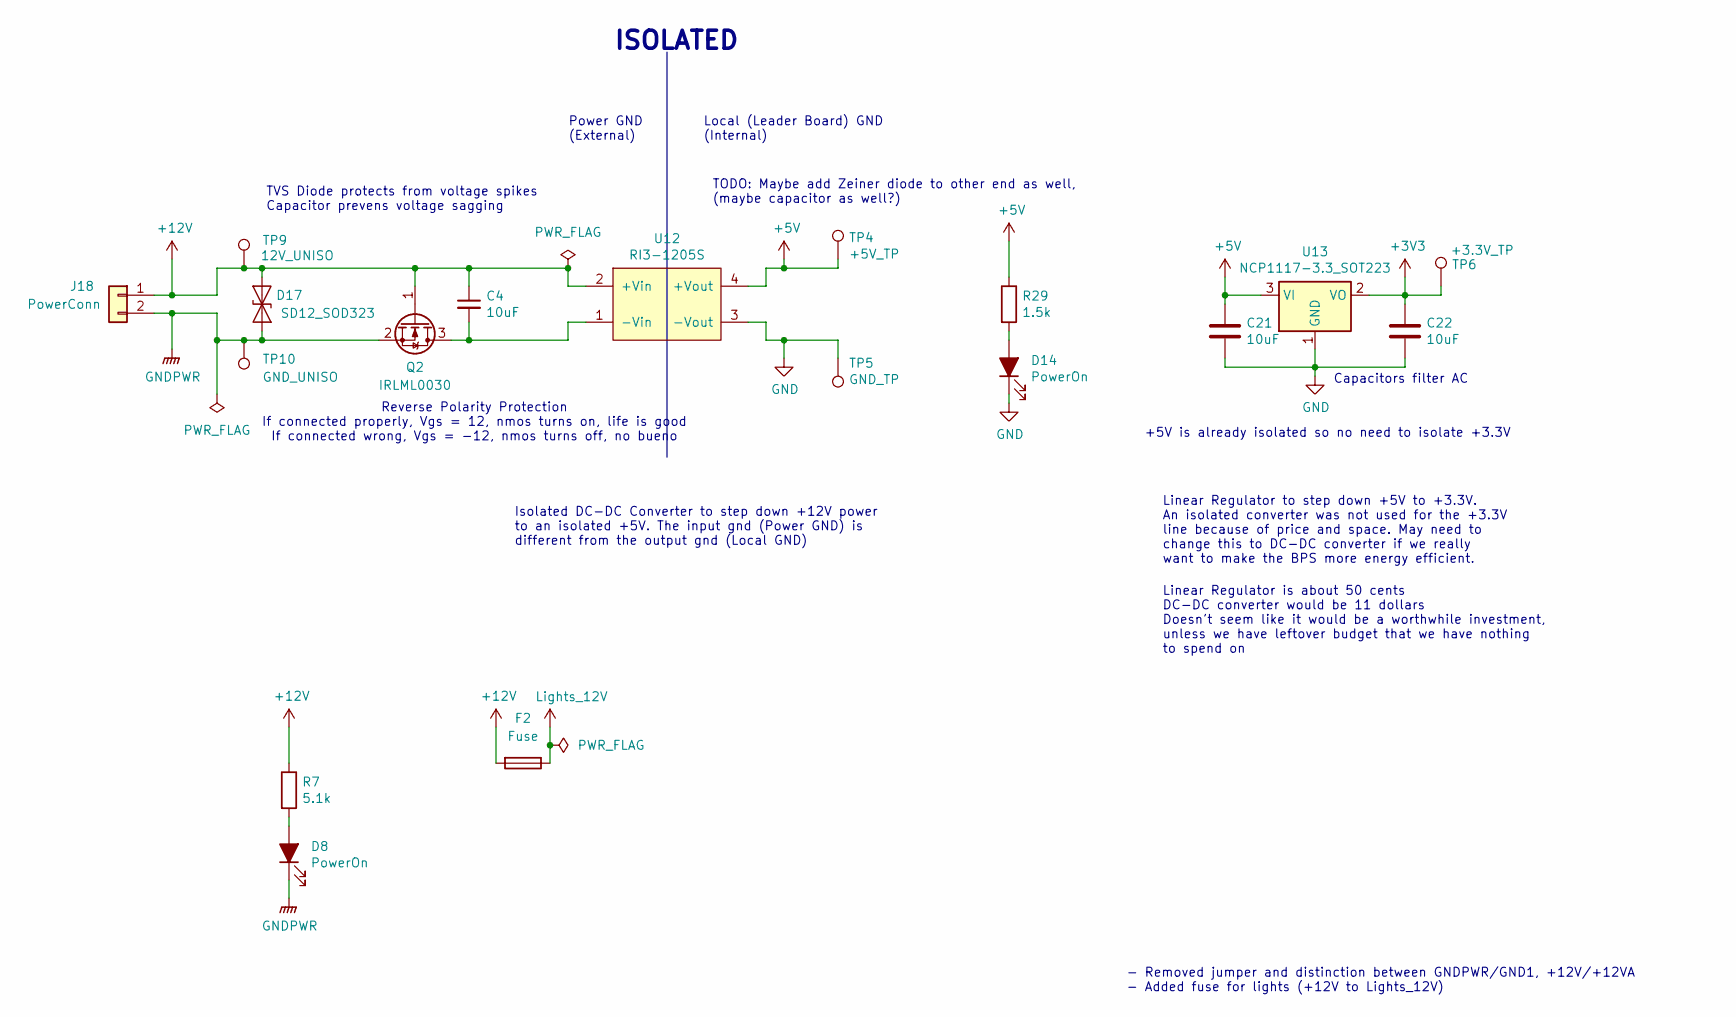
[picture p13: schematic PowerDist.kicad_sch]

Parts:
C4, C21, C22: 10uF; C_0805_2012Metric; Mouser Part Number 963-TMK212BBJ106MGHT
D8, D14: PowerOn; LED_0805_2012Metric; Mouser Part Number 604-APTD2012LCGCK
D17: SD12_SOD323; D_SOD-323
F2: Fuse; Fuse_1206_3216Metric; Mouser Part Number 576-0440003.WR
J18: PowerConn; Molex_MicroFit3.0_1x2xP3.00mm_PolarizingPeg_Vertical
Q2: IRLML0030; SOT-23
R7: 5.1k; R_0805_2012Metric
R29: 1.5k; R_0805_2012Metric; Mouser Part Number 71-CRCW08051K50JNEB
TP4: +5V_TP; TestPoint_Keystone_5005-5009_Compact
TP5: GND_TP; TestPoint_Keystone_5005-5009_Compact
TP6: +3.3V_TP; TestPoint_Keystone_5005-5009_Compact
TP9: 12V_UNISO; TestPoint_Keystone_5005-5009_Compact
TP10: GND_UNISO; TestPoint_Keystone_5005-5009_Compact
U12: RI3-1205S; RI3_DC_Converter; Mouser Part Number 919-RI3-1205S
U13: NCP1117-3.3_SOT223; SOT-223-3_TabPin2; Mouser Part Number 863-NCP1117ST33T3G

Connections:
+3V3: C22.1, TP6.1, U13.2 (VO); also elsewhere on the board
+5V: C21.1, R29.1, TP4.1, U12.4 (+Vout), U13.3 (VI); also elsewhere on the board
+12V: C4.1, D17.2 (A2), F2.2, J18.1, Q2.1 (G), R7.1, TP9.1, U12.2 (+Vin); also elsewhere on the board
GND: C21.2, C22.2, D14.1 (K), TP5.1, U12.3 (-Vout), U13.1 (GND); also elsewhere on the board
GNDPWR: D8.1 (K), D17.1 (A1), J18.2, Q2.2 (S), TP10.1; also elsewhere on the board
Lights_12V: F2.1; also elsewhere on the board
unnamed: D8.2 (A), R7.2
unnamed: D14.2 (A), R29.2
unnamed: C4.2, Q2.3 (D), U12.1 (-Vin)

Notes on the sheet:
Isolated DC-DC Converter to step down +12V power to an isolated +5V. The input gnd (Power GND) is different from the output gnd (Local GND)
TODO: Maybe add Zeiner diode to other end as well, (maybe capacitor as well?)
Linear Regulator to step down +5V to +3.3V. An isolated converter was not used for the +3.3V line because of price and space. May need to change this to DC-DC converter if we really want to make the BPS more energy efficient.
Local (Leader Board) GND (Internal)
Linear Regulator is about 50 cents DC-DC converter would be 11 dollars Doesn't seem like it would be a worthwhile investment, unless we have leftover budget that we have nothing to spend on
+5V is already isolated so no need to isolate +3.3V
Power GND (External)
ISOLATED
TVS Diode protects from voltage spikes Capacitor prevens voltage sagging
Capacitors filter AC
- Removed jumper and distinction between GNDPWR/GND1, +12V/+12VA - Added fuse for lights (+12V to Lights_12V)
Reverse Polarity Protection If connected properly, Vgs = 12, nmos turns on, life is good If connected wrong, Vgs = -12, nmos turns off, no bueno

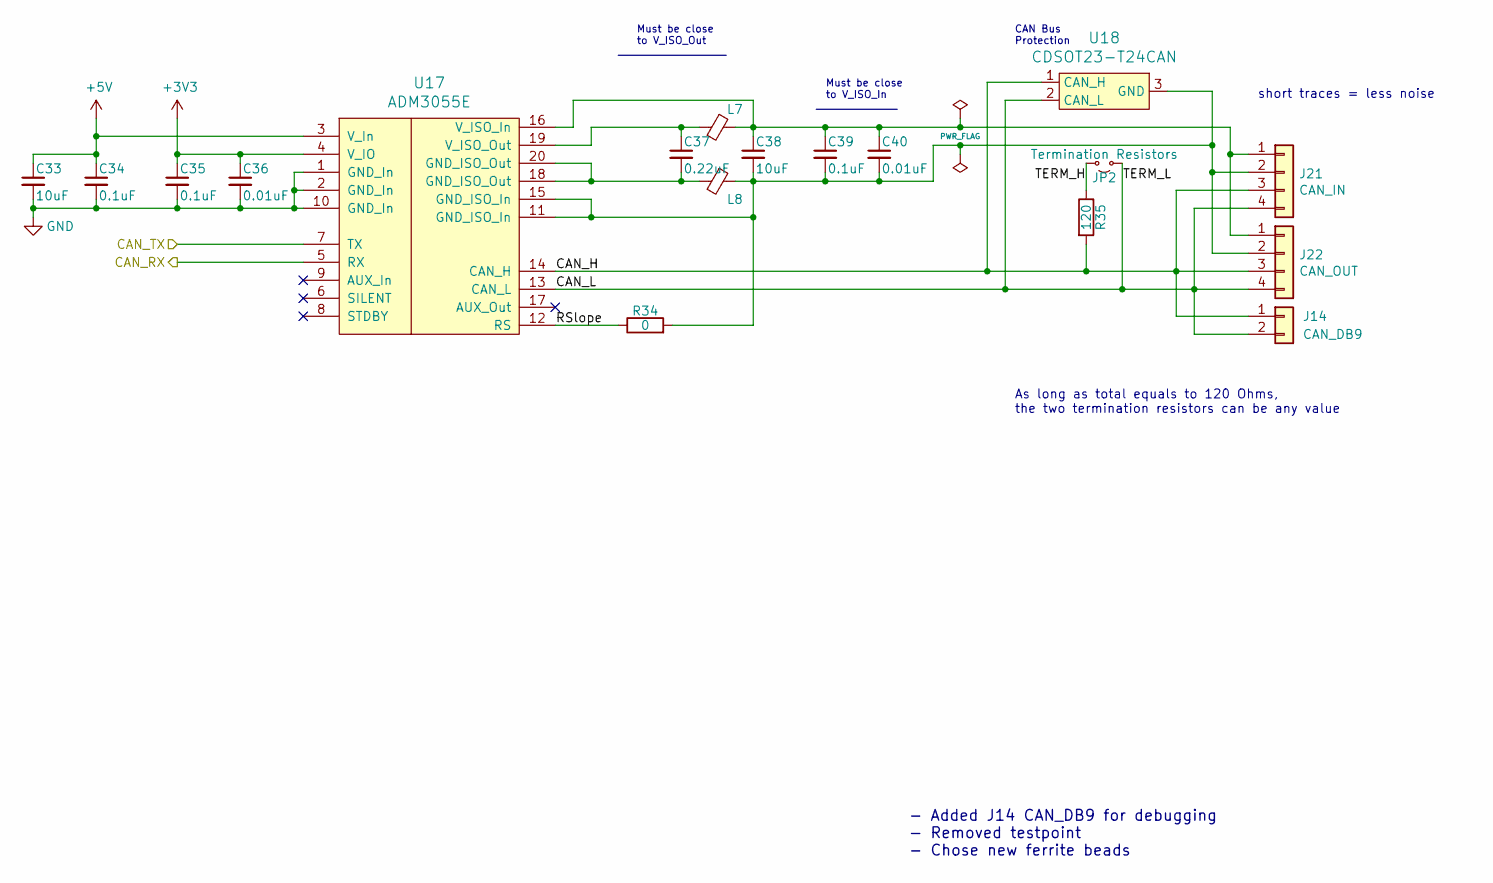
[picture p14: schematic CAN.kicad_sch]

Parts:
C33, C38: 10uF; C_0805_2012Metric; Mouser Part Number 963-TMK212BBJ106MGHT
C34, C35, C39: 0.1uF; C_0805_2012Metric; Mouser Part Number 80-C0805C104M5R
C36, C40: 0.01uF; C_0805_2012Metric
C37: 0.22uF; C_0805_2012Metric; Mouser Part Number 80-C0805C224J1RECTU
J14: CAN_DB9; Molex_Micro-Fit_3.0_43650-0215_1x02_P3.00mm_Vertical
J21: CAN_IN; Molex_MicroFit3.0_1x4xP3.00mm_PolarizingPeg_Vertical
J22: CAN_OUT; Molex_MicroFit3.0_1x4xP3.00mm_PolarizingPeg_Vertical
JP2: Termination Resistors; PinHeader_1x02_P2.54mm_Vertical
L7, L8: 1.8k; L_0805_2012Metric; Mouser Part Number 710-742792090
R34: 0; R_0805_2012Metric; Mouser Part Number 71-CRCW08050000Z0EAC
R35: 120; R_0805_2012Metric
U17: ADM3055E; SOIC-20W_7.5x15.4mm_Pitch1.27mm
U18: CDSOT23-T24CAN; SOT-23-3; Mouser Part Number 652-CDSOT23-T24CAN

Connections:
+3V3: C35.1, C36.1, U17.4 (V_IO); also elsewhere on the board
+5V: C33.1, C34.1, U17.3 (V_In); also elsewhere on the board
/CAN_Rx: U17.5 (RX); also elsewhere on the board
/CAN_Tx: U17.7 (TX); also elsewhere on the board
/Car_CAN/CAN_H: J14.1, J21.3, J22.3, R35.2, U17.14 (CAN_H), U18.1 (CAN_H)
/Car_CAN/CAN_L: J14.2, J21.4, J22.4, JP2.1 (A), U17.13 (CAN_L), U18.2 (CAN_L)
/Car_CAN/RSlope: R34.1, U17.12 (RS)
/Car_CAN/TERM_H: JP2.2 (B), R35.1
GND: C33.2, C34.2, C35.2, C36.2, U17.1 (GND_In), U17.2 (GND_In), U17.10 (GND_In); also elsewhere on the board
unnamed: C37.2, L8.2, U17.18 (GND_ISO_Out), U17.20 (GND_ISO_Out)
unnamed: C38.1, C39.1, C40.1, J21.1, J22.1, L7.1, U17.16 (V_ISO_In)
unnamed: C38.2, C39.2, C40.2, J21.2, J22.2, L8.1, R34.2, U17.11 (GND_ISO_In), U17.15 (GND_ISO_In), U18.3 (GND)
unnamed: C37.1, L7.2, U17.19 (V_ISO_Out)

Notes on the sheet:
short traces = less noise
CAN Bus Protection
As long as total equals to 120 Ohms, the two termination resistors can be any value
Must be close to V_ISO_Out
Must be close to V_ISO_In
- Added J14 CAN_DB9 for debugging - Removed testpoint - Chose new ferrite beads

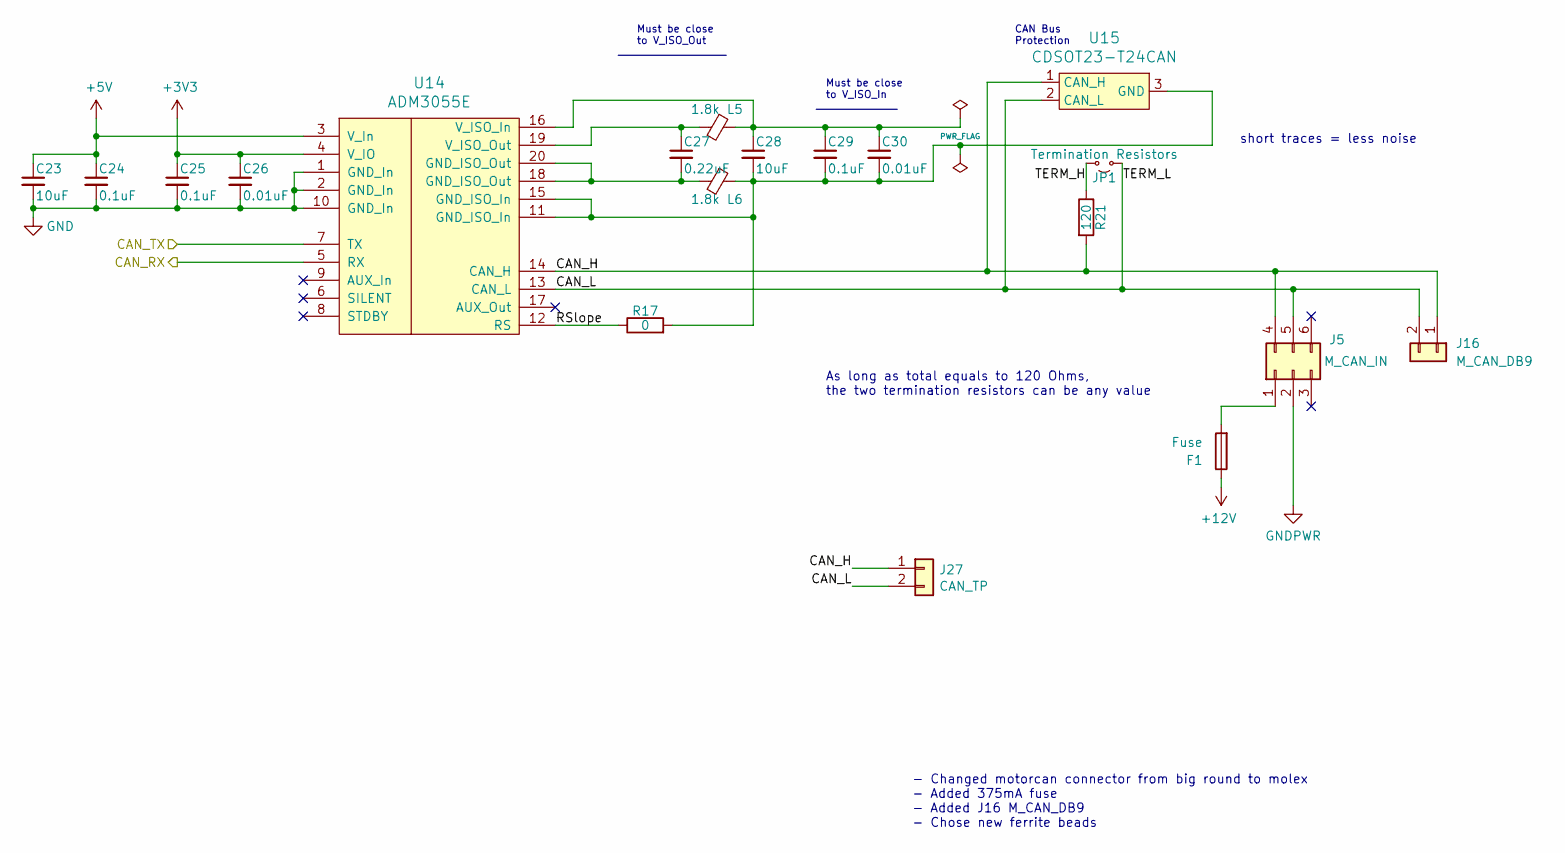
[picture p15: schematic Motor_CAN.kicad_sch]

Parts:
C23, C28: 10uF; C_0805_2012Metric; Mouser Part Number 963-TMK212BBJ106MGHT
C24, C25, C29: 0.1uF; C_0805_2012Metric; Mouser Part Number 80-C0805C104M5R
C26, C30: 0.01uF; C_0805_2012Metric
C27: 0.22uF; C_0805_2012Metric; Mouser Part Number 80-C0805C224J1RECTU
F1: Fuse; Fuse_1206_3216Metric; Mouser Part Number 576-0440.375WR
J5: M_CAN_IN; Molex_Micro-Fit_3.0_43045-0612_2x03_P3.00mm_Vertical
J16: M_CAN_DB9; Molex_Micro-Fit_3.0_43650-0215_1x02_P3.00mm_Vertical
J27: CAN_TP; PinHeader_1x02_P2.54mm_Vertical
JP1: Termination Resistors; PinHeader_1x02_P2.54mm_Vertical
L5, L6: 1.8k; L_0805_2012Metric; Mouser Part Number 710-742792090
R17: 0; R_0805_2012Metric; Mouser Part Number 71-CRCW08050000Z0EAC
R21: 120; R_0805_2012Metric
U14: ADM3055E; SOIC-20W_7.5x15.4mm_Pitch1.27mm
U15: CDSOT23-T24CAN; SOT-23-3; Mouser Part Number 652-CDSOT23-T24CAN

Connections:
+3V3: C25.1, C26.1, U14.4 (V_IO); also elsewhere on the board
+5V: C23.1, C24.1, U14.3 (V_In); also elsewhere on the board
+12V: F1.1; also elsewhere on the board
/MotorCAN_Rx: U14.5 (RX); also elsewhere on the board
/MotorCAN_Tx: U14.7 (TX); also elsewhere on the board
/Motor_CAN/CAN_H: J5.4, J16.1, J27.1, R21.2, U14.14 (CAN_H), U15.1 (CAN_H)
/Motor_CAN/CAN_L: J5.5, J16.2, J27.2, JP1.1 (A), U14.13 (CAN_L), U15.2 (CAN_L)
/Motor_CAN/RSlope: R17.1, U14.12 (RS)
/Motor_CAN/TERM_H: JP1.2 (B), R21.1
GND: C23.2, C24.2, C25.2, C26.2, U14.1 (GND_In), U14.2 (GND_In), U14.10 (GND_In); also elsewhere on the board
GNDPWR: J5.2; also elsewhere on the board
unnamed: C27.2, L6.2, U14.18 (GND_ISO_Out), U14.20 (GND_ISO_Out)
unnamed: F1.2, J5.1
unnamed: C28.1, C29.1, C30.1, L5.1, U14.16 (V_ISO_In)
unnamed: C27.1, L5.2, U14.19 (V_ISO_Out)
unnamed: C28.2, C29.2, C30.2, L6.1, R17.2, U14.11 (GND_ISO_In), U14.15 (GND_ISO_In), U15.3 (GND)

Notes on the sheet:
Must be close to V_ISO_Out
Must be close to V_ISO_In
short traces = less noise
As long as total equals to 120 Ohms, the two termination resistors can be any value
- Changed motorcan connector from big round to molex - Added 375mA fuse - Added J16 M_CAN_DB9 - Chose new ferrite beads
CAN Bus Protection

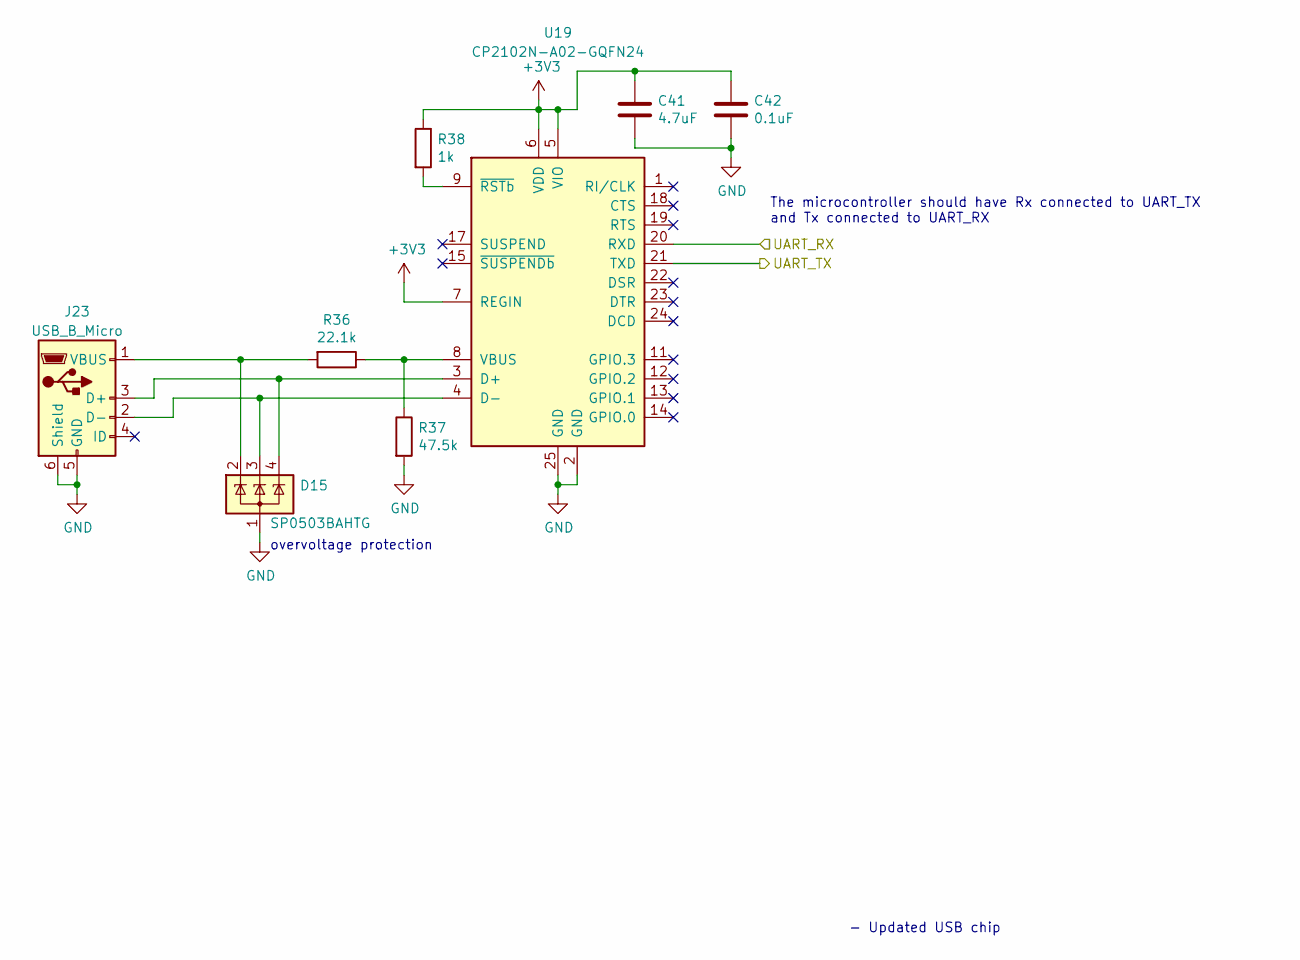
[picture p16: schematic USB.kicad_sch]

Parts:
C41: 4.7uF; C_0805_2012Metric; Mouser Part Number 81-GRM219R6YA475KA3D
C42: 0.1uF; C_0805_2012Metric; Mouser Part Number 80-C0805C104M5R
D15: SP0503BAHTG; SOT-143; Mouser Part Number 576-SP0503BAHTG
J23: USB_B_Micro; USB_Micro-B_Molex-105017-0001; Mouser Part Number 538-105017-1001
R36: 22.1k; R_0805_2012Metric; Mouser Part Number 71-CRCW0805-22.1K-E3
R37: 47.5k; R_0805_2012Metric; Mouser Part Number 71-CRCW0805-47.5K-E3
R38: 1k; R_0805_2012Metric; Mouser Part Number 71-CRCW08051K00FKEAC
U19: CP2102N-A02-GQFN24; QFN-24-1EP_4x4mm_P0.5mm_EP2.6x2.6mm; Mouser Part Number 634-CP2102NA01GQFN24

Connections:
+3V3: C41.1, C42.1, R38.1, U19.5 (VIO), U19.6 (VDD), U19.7 (REGIN); also elsewhere on the board
/USART2_Rx: U19.21 (TXD); also elsewhere on the board
/USART2_Tx: U19.20 (RXD); also elsewhere on the board
GND: C41.2, C42.2, D15.1 (A), J23.5 (GND), J23.6 (Shield), R37.2, U19.2 (GND), U19.25 (GND); also elsewhere on the board
unnamed: D15.4 (K), J23.3 (D+), U19.3 (D+)
unnamed: D15.3 (K), J23.2 (D-), U19.4 (D-)
unnamed: D15.2 (K), J23.1 (VBUS), R36.2
unnamed: R36.1, R37.1, U19.8 (VBUS)
unnamed: R38.2, U19.9 (~RSTb)

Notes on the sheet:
- Updated USB chip
The microcontroller should have Rx connected to UART_TX and Tx connected to UART_RX
overvoltage protection

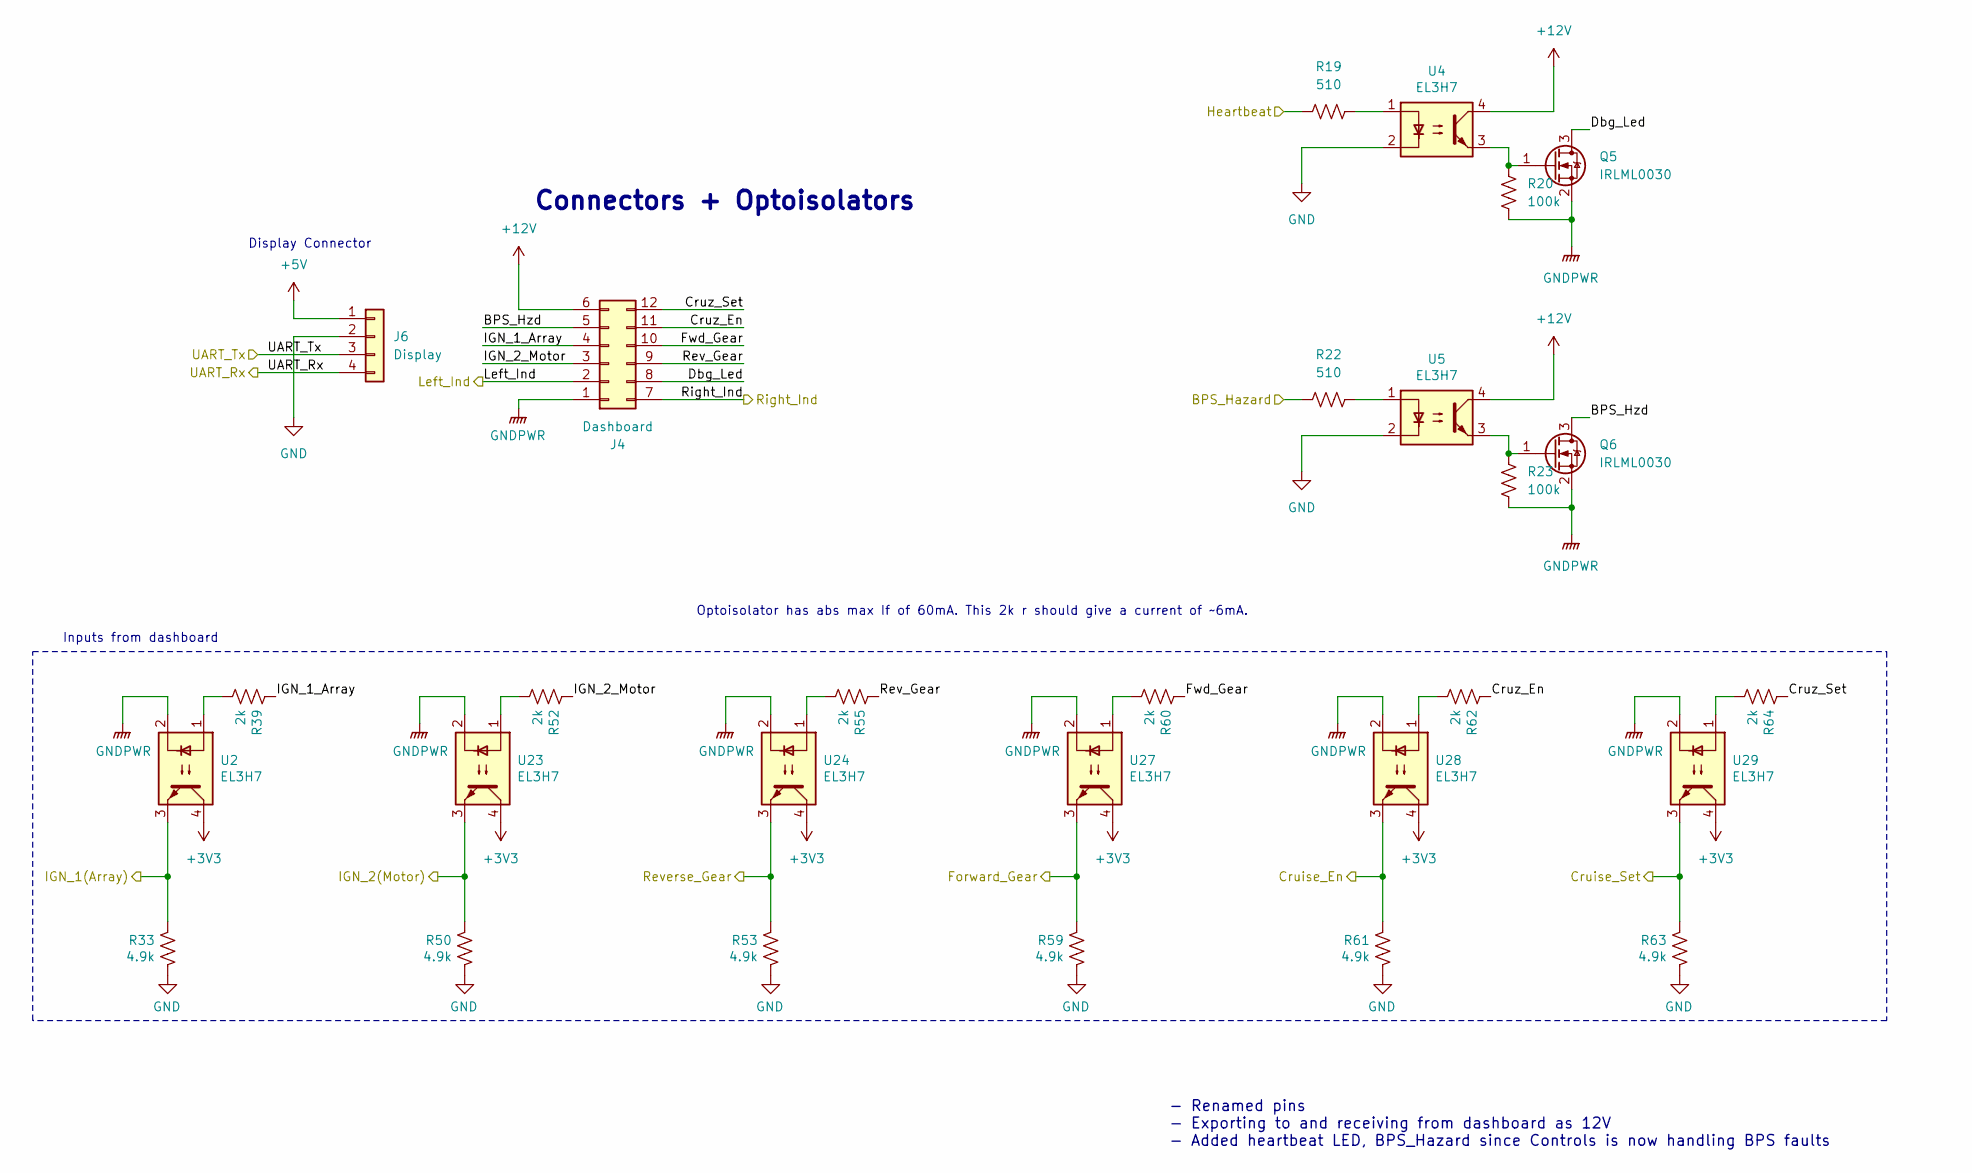
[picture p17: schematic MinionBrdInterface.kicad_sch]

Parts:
J4: Dashboard; Molex_MicroFit3.0_2x6xP3.00mm_PolarizingPeg_Vertical
J6: Display; Molex_Micro-Fit_3.0_43650-0415_1x04_P3.00mm_Vertical
Q5, Q6: IRLML0030; SOT-23
R19, R22: 510; R_0805_2012Metric; Mouser Part Number 71-CRCW0805510RFKEAC
R20, R23: 100k; R_0805_2012Metric; Mouser Part Number 71-CRCW0805100KFKEAC
R33, R50, R53, R59, R61, R63: 4.9k; R_0805_2012Metric; Mouser Part Number 71-CRCW08054K99FKEAC
R39, R52, R55, R60, R62, R64: 2k; R_0805_2012Metric; Mouser Part Number 71-CRCW08052K00FKEC
U2, U4, U5, U23, U24, U27, U28, U29: EL3H7; SSOP-4_4.4x2.6mm_P1.27mm; Mouser Part Number 638-EL3H7DTAVG

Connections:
+3V3: U2.4, U23.4, U24.4, U27.4, U28.4, U29.4; also elsewhere on the board
+5V: J6.1; also elsewhere on the board
+12V: J4.6, U4.4, U5.4; also elsewhere on the board
/Bps_Hazard: R22.1; also elsewhere on the board
/Cruise_En: R61.1, U28.3; also elsewhere on the board
/Cruise_Set: R63.1, U29.3; also elsewhere on the board
/DashAndDisplay/BPS_Hzd: J4.5, Q6.3 (D)
/DashAndDisplay/Cruz_En: J4.11, R62.1
/DashAndDisplay/Cruz_Set: J4.12, R64.1
/DashAndDisplay/Dbg_Led: J4.8, Q5.3 (D)
/DashAndDisplay/Fwd_Gear: J4.10, R60.1
/DashAndDisplay/IGN_1_Array: J4.4, R39.1
/DashAndDisplay/IGN_2_Motor: J4.3, R52.1
/DashAndDisplay/Rev_Gear: J4.9, R55.1
/Forward: R59.1, U27.3; also elsewhere on the board
/Heartbeat: R19.1; also elsewhere on the board
/IG1: R33.1, U2.3; also elsewhere on the board
/IG2: R50.1, U23.3; also elsewhere on the board
/Left_Ind: J4.2; also elsewhere on the board
/Reverse: R53.1, U24.3; also elsewhere on the board
/Right_Ind: J4.7; also elsewhere on the board
/UART4_Rx: J6.4; also elsewhere on the board
/UART4_Tx: J6.3; also elsewhere on the board
GND: J6.2, R33.2, R50.2, R53.2, R59.2, R61.2, R63.2, U4.2, U5.2; also elsewhere on the board
GNDPWR: J4.1, Q5.2 (S), Q6.2 (S), R20.2, R23.2, U2.2, U23.2, U24.2, U27.2, U28.2, U29.2; also elsewhere on the board
unnamed: Q5.1 (G), R20.1, U4.3
unnamed: Q6.1 (G), R23.1, U5.3
unnamed: R19.2, U4.1
unnamed: R22.2, U5.1
unnamed: R39.2, U2.1
unnamed: R52.2, U23.1
unnamed: R55.2, U24.1
unnamed: R60.2, U27.1
unnamed: R62.2, U28.1
unnamed: R64.2, U29.1

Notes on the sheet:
- Renamed pins - Exporting to and receiving from dashboard as 12V - Added heartbeat LED, BPS_Hazard since Controls is now handling BPS faults
Connectors + Optoisolators
Inputs from dashboard
Display Connector
Optoisolator has abs max If of 60mA. This 2k r should give a current of ~6mA.

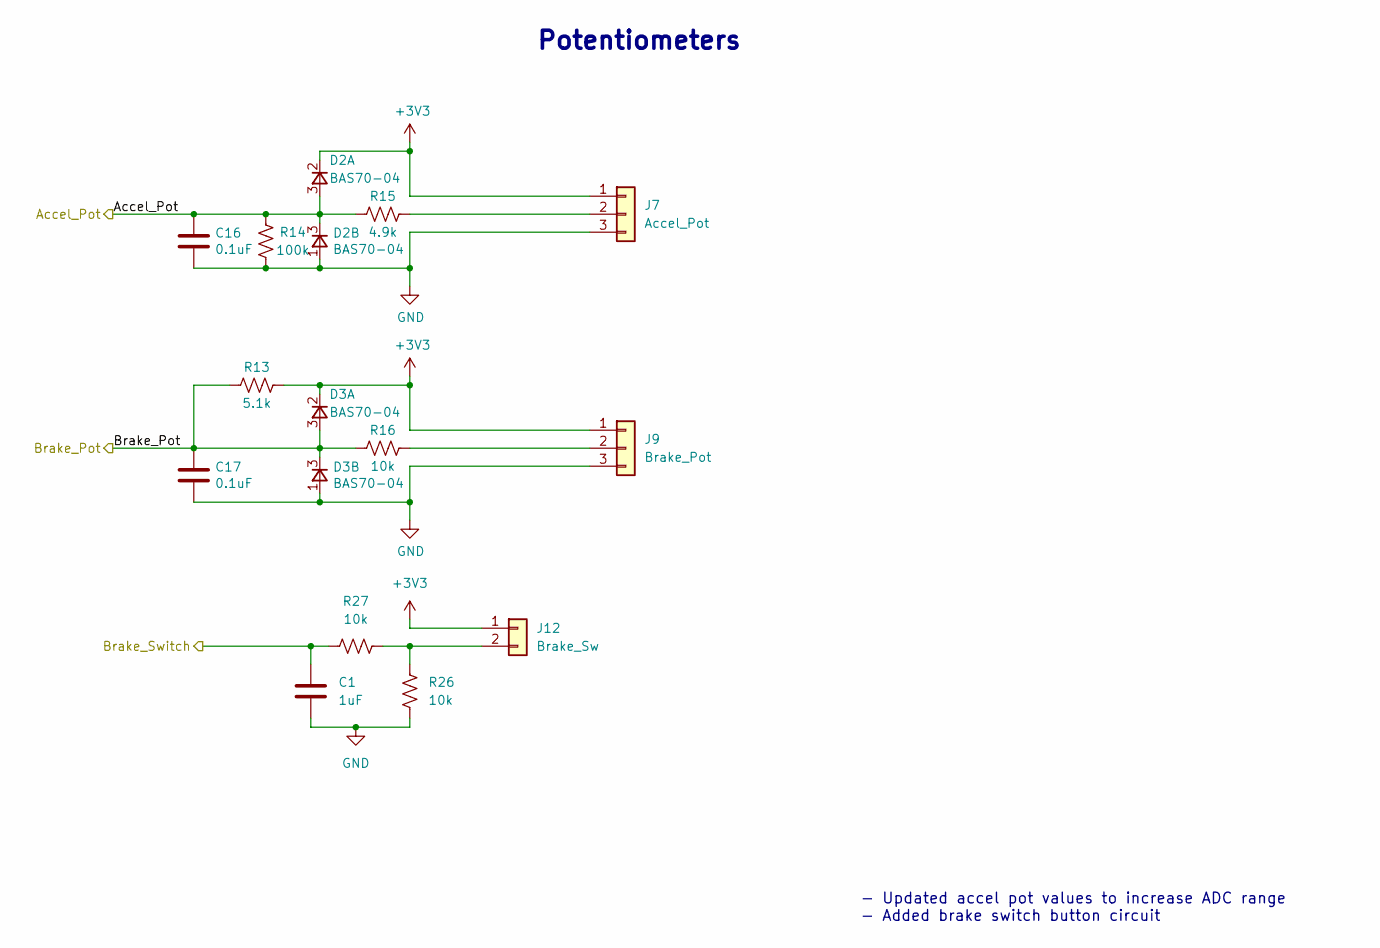
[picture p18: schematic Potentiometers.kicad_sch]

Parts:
C1: 1uF; C_0805_2012Metric
C16, C17: 0.1uF; C_0805_2012Metric; Mouser Part Number 80-C0805C104M5R
D2, D3: BAS70-04; SOT-23; Mouser Part Number 652-CDSOT23-T24CAN
J7: Accel_Pot; Molex_Micro-Fit_3.0_43650-0315_1x03_P3.00mm_Vertical
J9: Brake_Pot; Molex_Micro-Fit_3.0_43650-0315_1x03_P3.00mm_Vertical
J12: Brake_Sw; Molex_Micro-Fit_3.0_43650-0215_1x02_P3.00mm_Vertical
R13: 5.1k; R_0805_2012Metric
R14: 100k; R_0805_2012Metric; Mouser Part Number 71-CRCW0805100KFKEAC
R15: 4.9k; R_0805_2012Metric; Mouser Part Number 71-CRCW08054K99FKEAC
R16, R26, R27: 10k; R_0805_2012Metric; Mouser Part Number 71-CRCW080510K0FKEAC

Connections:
+3V3: D2.2, D3.2, J7.1, J9.1, J12.1, R13.1; also elsewhere on the board
/Accel_Pot: C16.1, D2.3, R14.1, R15.2; also elsewhere on the board
/Brake_Pot: C17.1, D3.3, R13.2, R16.2; also elsewhere on the board
/Brake_SW: C1.1, R27.1; also elsewhere on the board
GND: C1.2, C16.2, C17.2, D2.1, D3.1, J7.3, J9.3, R14.2, R26.2; also elsewhere on the board
unnamed: J7.2, R15.1
unnamed: J9.2, R16.1
unnamed: J12.2, R26.1, R27.2

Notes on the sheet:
Potentiometers
- Updated accel pot values to increase ADC range - Added brake switch button circuit

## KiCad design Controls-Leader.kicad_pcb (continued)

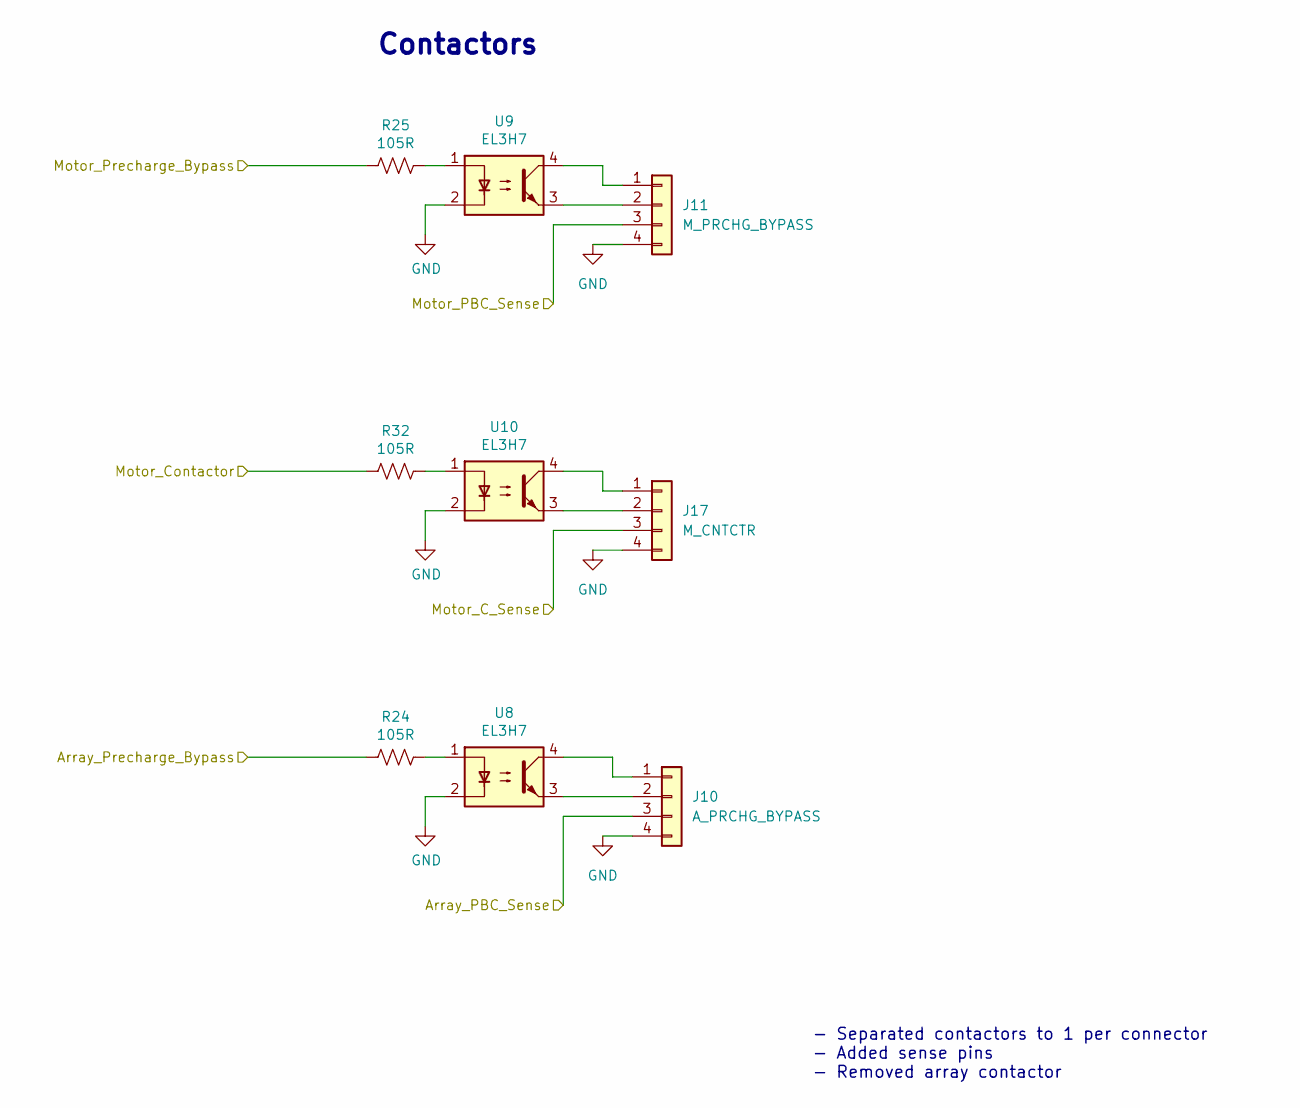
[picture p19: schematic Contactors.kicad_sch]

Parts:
J10: A_PRCHG_BYPASS; Molex_Micro-Fit_3.0_43650-0415_1x04_P3.00mm_Vertical
J11: M_PRCHG_BYPASS; Molex_Micro-Fit_3.0_43650-0415_1x04_P3.00mm_Vertical
J17: M_CNTCTR; Molex_Micro-Fit_3.0_43650-0415_1x04_P3.00mm_Vertical
R24, R25, R32: 105R; R_0805_2012Metric; Mouser Part Number 71-CRCW0805105RFKEA
U8, U9, U10: EL3H7; SSOP-4_4.4x2.6mm_P1.27mm; Mouser Part Number 638-EL3H7DTAVG

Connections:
/Array_PBC_Sense: J10.3; also elsewhere on the board
/Array_PRCHG_Bypass: R24.2; also elsewhere on the board
/Motor_C_Sense: J17.3; also elsewhere on the board
/Motor_Contactor: R32.2; also elsewhere on the board
/Motor_PBC_Sense: J11.3; also elsewhere on the board
/Motor_PRCHG_Bypass: R25.2; also elsewhere on the board
GND: J10.4, J11.4, J17.4, U8.2, U9.2, U10.2; also elsewhere on the board
unnamed: J10.1, U8.4
unnamed: J10.2, U8.3
unnamed: J11.1, U9.4
unnamed: J11.2, U9.3
unnamed: J17.1, U10.4
unnamed: J17.2, U10.3
unnamed: R24.1, U8.1
unnamed: R25.1, U9.1
unnamed: R32.1, U10.1

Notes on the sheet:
Contactors
- Separated contactors to 1 per connector - Added sense pins - Removed array contactor

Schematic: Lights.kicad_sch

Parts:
LOGO4: UTSVT Logo; UTSVT_Logo_Symbol
R5, R10: 2k; R_0805_2012Metric; Mouser Part Number 71-CRCW08052K00FKEC
TP7: RIGHT_BLINK; TestPoint_Keystone_5005-5009_Compact
TP8: LEFT_BLINK; TestPoint_Keystone_5005-5009_Compact
U1, U6: EL3H7; SSOP-4_4.4x2.6mm_P1.27mm; Mouser Part Number 638-EL3H7DTAVG

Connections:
/Left_Ind: R10.2; also elsewhere on the board
/Lights/LEFT_BLINK: TP8.1, U1.3; also elsewhere on the board
/Lights/RIGHT_BLINK: TP7.1, U6.3; also elsewhere on the board
/Right_Ind: R5.2; also elsewhere on the board
/TimerCLK: U1.4, U6.4; also elsewhere on the board
GNDPWR: U1.2, U6.2; also elsewhere on the board
unnamed: R5.1, U6.1
unnamed: R10.1, U1.1

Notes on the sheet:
- Replaced lights drivers/circuits - Replaced 555 timer with blinking gpio that passes through to drivers when dashboard Left/Right 3-pos switch is toggled - Intended to connect to breakout boards that split out the necessary number of lights

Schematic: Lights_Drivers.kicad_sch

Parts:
BRAKELIGHT1: EXTERNAL_BRAKELIGHT; Molex_Micro-Fit_3.0_43650-0215_1x02_P3.00mm_Vertical
L_BLINK_EXT1: EXTERNAL_LEFTBLINK; Molex_Micro-Fit_3.0_43650-0215_1x02_P3.00mm_Vertical
Q1, Q3, Q4: IRLML0030; SOT-23
R6, R11, R12: 510; R_0805_2012Metric; Mouser Part Number 71-CRCW0805510RFKEAC
R41, R56, R58: 100k; R_0805_2012Metric; Mouser Part Number 71-CRCW0805100KFKEAC
R_BLINK_EXT1: EXTERNAL_RIGHTBLINK; Molex_Micro-Fit_3.0_43650-0215_1x02_P3.00mm_Vertical
U3, U25, U26: EL3H7; SSOP-4_4.4x2.6mm_P1.27mm; Mouser Part Number 638-EL3H7DTAVG

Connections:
/Brake_Light: R6.1; also elsewhere on the board
/Lights/LEFT_BLINK: R12.1; also elsewhere on the board
/Lights/RIGHT_BLINK: R11.1; also elsewhere on the board
GND: U3.2, U25.2, U26.2; also elsewhere on the board
GNDPWR: Q1.2 (S), Q3.2 (S), Q4.2 (S), R41.2, R56.2, R58.2; also elsewhere on the board
Lights_12V: BRAKELIGHT1.1, L_BLINK_EXT1.1, R_BLINK_EXT1.1, U3.4, U25.4, U26.4; also elsewhere on the board
unnamed: BRAKELIGHT1.2, Q4.3 (D)
unnamed: L_BLINK_EXT1.2, Q1.3 (D)
unnamed: Q1.1 (G), R56.1, U25.3
unnamed: Q3.3 (D), R_BLINK_EXT1.2
unnamed: Q3.1 (G), R58.1, U26.3
unnamed: Q4.1 (G), R41.1, U3.3
unnamed: R6.2, U3.1
unnamed: R11.2, U26.1
unnamed: R12.2, U25.1

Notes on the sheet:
Assuming that all external lights have I-Lim Res

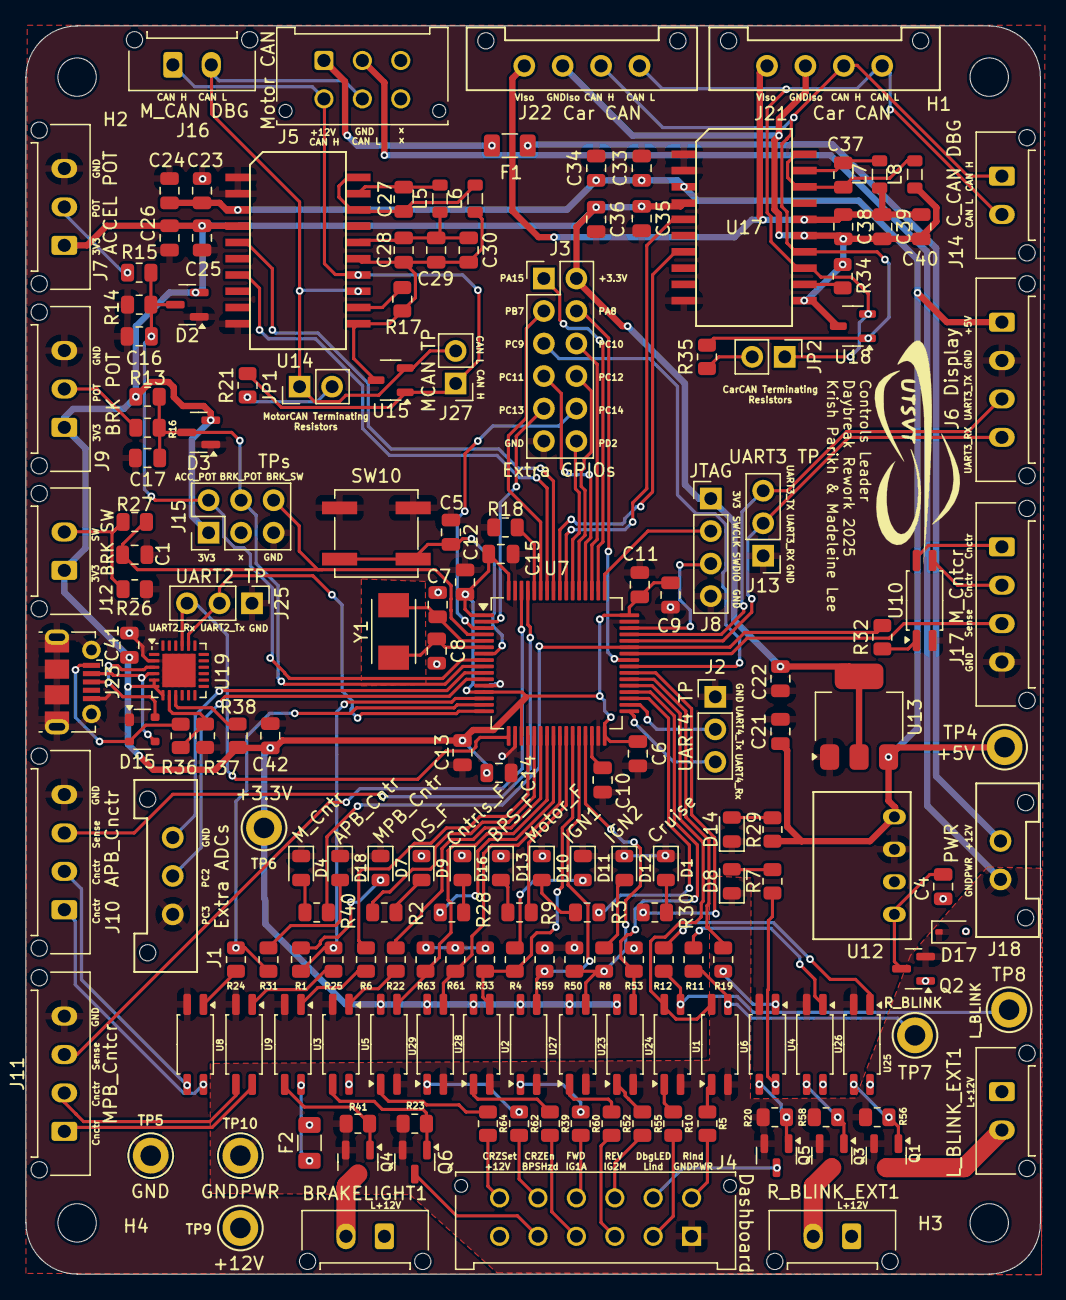
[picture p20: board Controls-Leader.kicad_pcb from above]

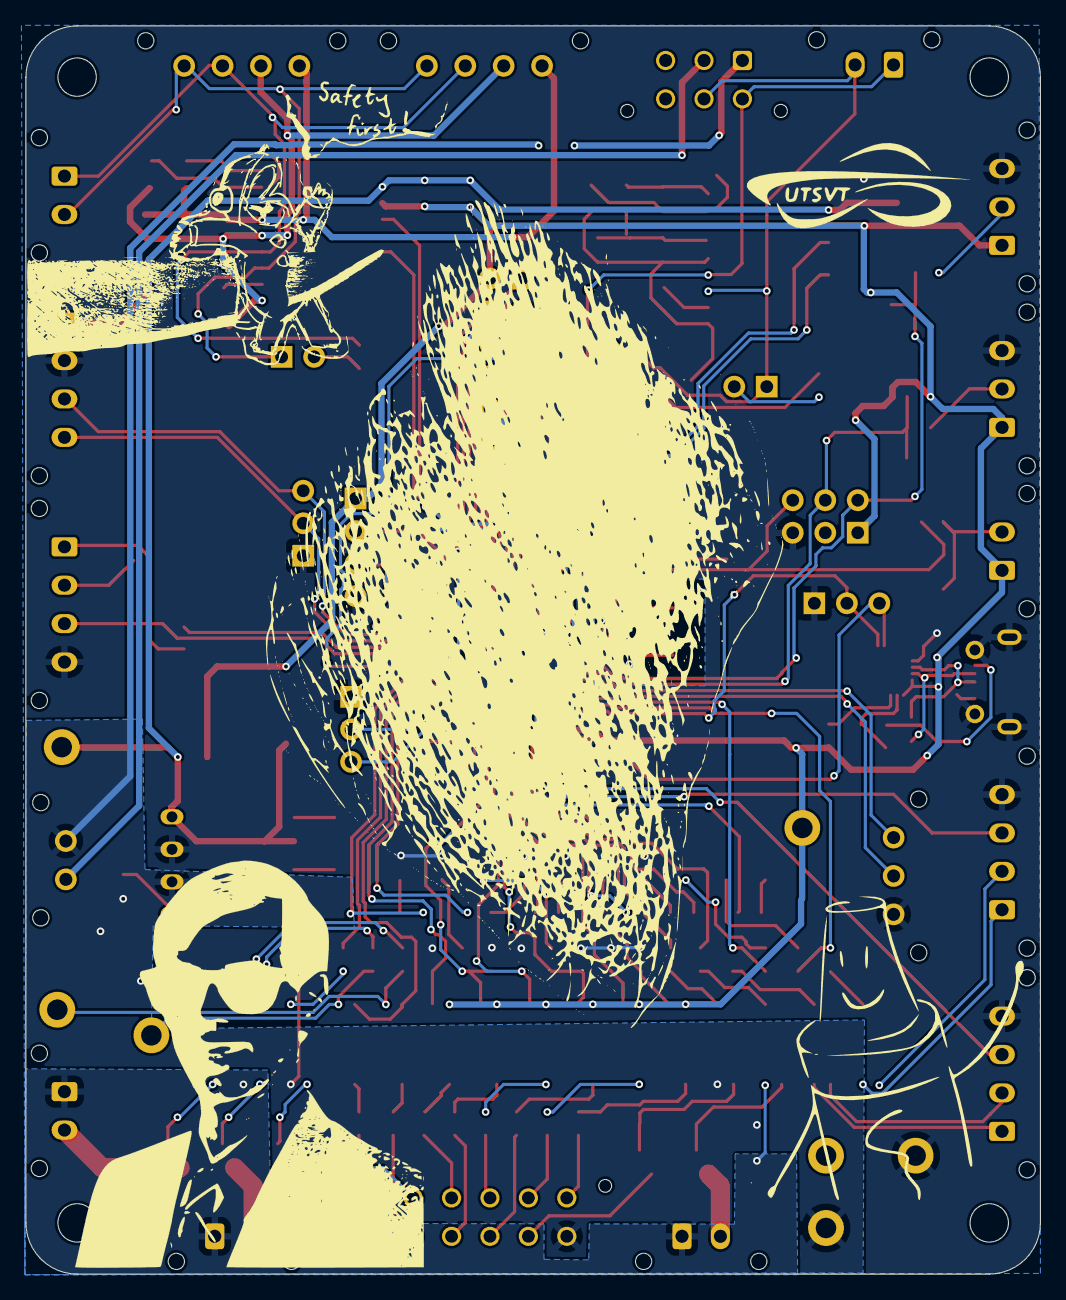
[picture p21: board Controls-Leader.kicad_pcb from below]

Board: 2 copper layers, 79.2 x 97.5 mm, 184 parts (2 on the bottom side), 139 nets.

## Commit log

2020-08-02 Set up for own repository
    [BOM.csv, BPS-Nucleo.kicad_pcb, BPS-Nucleo.sch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]
2020-08-08 Updates dashboard project to most recent version
    [BPSMaster.sch, CAN.sch, Contactor.kicad_pcb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]
2020-09-12 Edits schematic to make turn lights software controlled
    [Car-CAN.sch, Dashboard.sch, Motor_CAN.sch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]
2020-09-12 Updates PCB to add changes from the schematic
    [Dashboard.kicad_pcb, Dashboard.sch]
2020-09-19 Organizes the schematic into hierarchical sheets
    [CAN.sch, ControlSwitches.sch, Dashboard.sch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]
2020-09-19 Generates netlist and updates PCB components
    [Dashboard.kicad_pcb]
2020-09-19 Lays out CAN, power distribution, and power state indicator circuitry
    [Dashboard.kicad_pcb]
2020-09-27 Adds components for the shift register and lays out modularized components
    [CAN.sch, ExteriorLights.sch, IgnitionSwitch.sch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]
2020-09-27 Lays out PCB for Controls leader board
    [CAN.sch, Dashboard.kicad_pcb, Dashboard.sch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]
2020-10-01 Adds SPI header to test
    [Dashboard.kicad_pcb, MinionBrdInterface.sch]
2020-10-01 Makes all traces .25 mm
    [Dashboard.kicad_pcb]
2020-10-03 Labels sections and fixes DRC errors
    [Dashboard.kicad_pcb, MinionBrdInterface.sch]
2020-10-03 Adds labels to some connectors and edits layout to meet 0,2mm pad to trace clearance
    [Dashboard.kicad_pcb, Dashboard.sch, ExteriorLights.sch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]
2020-10-03 Finishes label and redesigns emergency switch/error light circuitry
    [Dashboard.kicad_pcb, IgnitionSwitch.sch]
2020-10-03 Adds connector for power secondary board
    [Dashboard.kicad_pcb, IgnitionSwitch.sch]
2020-10-03 Adds vias to extend ground plane
    [Dashboard.kicad_pcb]
2020-10-09 Makes the 12V and GNDPWR traces bigger
    [Dashboard.kicad_pcb, Potentiometers.sch]
2020-10-09 Extends the GND plane to under the potentiometers
    [Dashboard.kicad_pcb]
2020-10-09 Creates and then removes Gerbers
    [Dashboard.kicad_pcb]
2020-10-10 Add STEP file
    [Dashboard.kicad_pcb]
2020-12-12 Creates pdf of schematic
2020-12-19 Adds BPSPWR as a connection to the minion board and then fixes labels
    [Dashboard.kicad_pcb, Dashboard.sch, MinionBrdInterface.sch]
2021-01-10 Changes display power to 5V, puts fault LED on back, and adds gerbers
    [Dashboard-B_Cu.gbr, Dashboard-B_Mask.gbr, Dashboard-B_Paste.gbr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]
2021-01-23 Adds gerbers
    [Dashboard-B_Cu.gbr, Dashboard-B_Mask.gbr, Dashboard-B_Paste.gbr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]
2021-01-23 Updates Controls Leader PCB
    [Dashboard.kicad_pcb]
2021-02-06 3D models and resized rotary switch
    [Dashboard-B_Cu.gbr, Dashboard-B_Mask.gbr, Dashboard-B_Paste.gbr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]
2021-02-06 fixed merge changes with common
    [HX1188FNL.STEP]
2021-02-06 Cleans up folder and updates gerbers
    [Dashboard-B_Cu.gbr, Dashboard-B_Mask.gbr, Dashboard-B_Paste.gbr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]
2021-10-02 USB Tx/Rx, Crystal Keepout, 12V Separation, Can2-Can3, Motor CAN bus labels, Power Input Protection Circuitry
    [Dashboard.kicad_pcb, Dashboard.sch, ExteriorLights.sch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]
2021-10-03 Connects pots to ADC pins and removes JTAG connections
    [Dashboard.kicad_pcb, Dashboard.sch, IgnitionSwitch.sch]
2021-10-03 Flips exterior lights polarity on the connectors
    [Dashboard.kicad_pcb, ExteriorLights.sch]
2021-10-04 Updates gerbers and version number
    [Dashboard-B_Cu.gbr, Dashboard-B_Mask.gbr, Dashboard-B_Paste.gbr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]
2021-11-06 removes the isp
    [CAN.sch, Dashboard.kicad_pcb, Dashboard.sch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]
2021-11-06 removes isp
    [Dashboard.kicad_pcb]
2021-11-14 Changes the layout of the board, adds resistors for ignition switch, and gives motar can isolated +12v, still need to change resistor value for the isolated +12v(didnt remember how to find the value)
    [Dashboard.kicad_pcb, Dashboard.sch, ExteriorLights.sch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]
2021-11-16 Cleans up some of the traces in the power section
    [Dashboard.kicad_pcb, Dashboard.sch, PowerDist.sch]
2021-11-21 Adds backup camera
    [Dashboard.kicad_pcb, ExteriorLights.sch, MinionBrdInterface.sch]
2021-12-07 Updates gerbers and new controls leader
    [Dashboard-B_Cu.gbr, Dashboard-B_Mask.gbr, Dashboard-B_Paste.gbr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]
2022-02-21 Redo the board layout to be more compact.
    IMPORTANT: as of this moment, this is only a proposal for
    a new design, and the team has *not* determined whether
    this is necessary.
    This addresses some issues that I have had with the design
    of the Controls Leader board:
    - It is too bulky, and would be difficult to mount
    where it would be out of the way.
    - It requires the driver to physically interact with it,
    which could put unecessary strain on the board and
    further restrict the areas of the car where it could
    be mounted.
    - All of the connectors are on the back of the board,
    making it difficult to interact with during testing.
    Additionally, a strong effort has been made to main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
    [CAN.kicad_sch, Dashboard.kicad_pcb, Dashboard.kicad_sch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]
2022-04-02 Remove 12V isolator, swap CAN connector pins, etc.
    [CAN.kicad_sch, Dashboard.kicad_pcb, Dashboard.kicad_sch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]
2022-04-02 Release v2.4 and gerbers
    [Dashboard-B_Cu.gbr, Dashboard-B_Mask.gbr, Dashboard-B_Paste.gbr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]
2024-01-20 renamed Dash to Controls-Leader (#22)
    * renamed Dash to Controls-Leader
    * :)
    [Controls-Leader.kicad_pcb, Controls-Leader.kicad_sch, Controls-Leader.sch]
2024-04-06 added jlc bom assembly excel file
    [BOM for JLCPCB Assembly.xlsx, Controls-Leader.csv]
2025-02-01 Daybreak rework (#24)
    * Schematic notations for rework changes
    * Updated schematic in accordance to previous weeks annotated changes
    * Added .lck files to .gitignore.
    * Renamed Clk to PA5, removed CAN_TX/RX test points, deleted other .lck file and #auto_saved_files# (hopefully this does not break anything.
    * Changed testpoints to pin headers.
    * removed camera, fixed connectors, and changed status LEDS
    * Schematic finished :) hopefully not broken
    * Added back lights + drivers + timer for all blinkers and brake lights
    * Fuse added for motorCAN 12V
    * Renamed local net labels to be different from hierarchical ones in the MinionBrdInterface so that they aren't connected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
    [BOM for JLCPCB Assembly.xlsx, CAN.kicad_sch, Contactors.kicad_sch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]
2025-02-01 Added 3D models.
    [Controls-Leader.kicad_pcb]
2025-04-12 Schematic label fixing.
    [Controls-Leader.kicad_pcb, Controls-Leader.kicad_sch]
